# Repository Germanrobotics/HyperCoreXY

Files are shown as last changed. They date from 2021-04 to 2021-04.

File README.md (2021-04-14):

# HyperCoreXY

The HyperCoreXY is a DIY CoreXY Printer which aims for a large workspace while maintaining high printing speeds.

## Specification

- Stable aluminum extrusion frame
- Controlled via a Duet 2 Board
- Powerful 230V heated bed
- Print volume of 390x340x230mm
- Print speeds up to 80-100mm/s

## Todo

- [ ] BOM of all components used
- [ ] Complete assembly instructions
- [ ] A Housing for all electronics to clean things up
- [ ] Reduction of the weight of the Y-axis + Extruder to allow higher printing speeds

## Build Guide

Until I created assembly instructions, you will need to assemble the printer using these videos

**Part 1 Main Mechnical Assembly**
https://www.youtube.com/watch?v=HaM37b0eBO4

**Part 2 Electrical Assembly and first test**
https://www.youtube.com/watch?v=nZ0KHetVHEs

**Part 3 First Prints**
https://www.youtube.com/watch?v=0dgUXOkC-as

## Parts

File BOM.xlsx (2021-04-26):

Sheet: Printed Parts
Name | Description | Qty | Material
Printbed
Connectors print bed |  | 2 | PLA
Connectors print bed mirrored |  | 2 | PLA
Frame
Connector profile |  | 2 | PLA
Housing electronics |  | 1 | PLA
Extruder
Belt Tensioner |  | 2 | PLA
Cable holder |  | 1 | PLA
Cover holder extruder |  | 1 | PLA
Fan duct mirrored |  | 1 | PLA
Fan duct |  | 1 | PLA
Fan holder mirrored |  | 1 | PLA
Fan holder |  | 1 | PLA
Holder belt |  | 4 | PLA
Holder extruder |  | 1 | PLA
Holder hotend |  | 1 | PLA
Spacer 10mm |  | 2 | PLA
X-Axis
End stop X-axis |  | 1 | PLA
Y-Axis
Belt guide left |  | 1 | PLA
Belt guide right |  | 1 | PLA
Holder limit switch Y-axis |  | 2 | PLA
Holder X-axis |  | 2 | PLA
Motor holder left part 1 |  | 1 | PLA
Motor holder left part 2 |  | 1 | PLA
Motor holder right part 1 |  | 1 | PLA
Motor holder right part 2 |  | 1 | PLA
Spacer 6mm |  | 2 | PLA
Z-Axis
Holder bearing spindle |  | 2 | PLA
Holder limit switch Z-axis |  | 1 | PLA
Holder linear rails long |  | 1 | PLA
Holder linear rails |  | 2 | PLA
Motor holder Z-axis |  | 1 | PLA
Other Parts
Adapter 3mm to 5mm |  | 5 | PLA
Adapter 6 to 8mm | If you use the same motors as I do, you will need these | 3 | PLA

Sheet: Hardware
Name | Description | Qty
Angle 20x20 | For the aluminum extrusion | 32
Slot nuts M3 | More then needed | 100
Slot nuts M5 | More then needed | 150
Aluminum plate 430x430mm | 3 or 4mm thick, used as printbed | 1
Spring 20x7.5mm | Needed for the bed | 4
Nanotec 4T5618S2404-A | Stepper motor, but you can also use a Nema 17 or 23, but then you have to change the motor mounts | 4
Micro switches PANASONIC AV3724613-A | or similar, but you may need to adjust the mounts | 3
Belt pulley GT2 20T 8mm | used on motors and spindles, needs the 6mm to 8mm adapter, if you use nema 17 or 23 stepper, you need a different adapter | 5
Belt Idler GT2 20T 3mm | Idler with tooths | 6
Idler GT2 5mm | Idler without tooths, needs the 5mm to 3mm adapter | 5
Lead screw 350mm | 8mm diameter, I got a set with two horizontal bearings, you may need to buy them separately | 2
Linear bearing 350mm | MGN12H Linear bearings with one wagon | 3
Linear bearing 450mm | MGN12H Linear bearings with one wagon | 3
GT2 Belt 1000mm 500T | Closed GT2 Belt with 500Tooths, 1000mm long | 1
Bondtech BMG Extruder right | or a clone | 1
E3D Volcano Hotend Direct Drive | 12V Kit or a clone | 1
Nema 17 Pancake Stepper | used for the BMG Extruder | 1
PTFE Tubing | PTFE Tubing 1.75mm, you need around 80cm | 1
BL Touch | not necessary, but simplifies bedleveling | 1
GT2 Belt open | measured in meters | 6
Radial Fans | 5015 12V Radial Fans, used for part cooling | 2
Cylinder head screw M3x35 | More then needed | 50
Cylinder head screw M3x8 | More then needed | 100
Cylinder head screw M3x20 | More then needed | 50
Cylinder head screw M4x45 | More then needed | 50
Cylinder head screw M5x10 | More then needed | 150
Duet 2 Ethernet Board |  | 1
Power supply 12V 20A 240W | probably way too big, but it was the smallest I found | 1
Heated bed 220V 650W 408x408mm | i bought a yourDroid silicone heat bed | 1
Solid State Relay 220V 40A |  | 1

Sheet: Aluminum extrusion
Name | Length | Qty | I bought 11 1 meter long 20x20 Alumimun profiles and then cut them to length
Profil Print bed 1 | 420 | 2
Profil Print bed 2 | 350 | 2
Profil Frame 1 | 550 | 4
Profil Frame 2 | 370 | 3
Profil Frame 3 | 440 | 4
Profil Frame 4 | 520 | 5
Profil X-Axis | 510 | 1

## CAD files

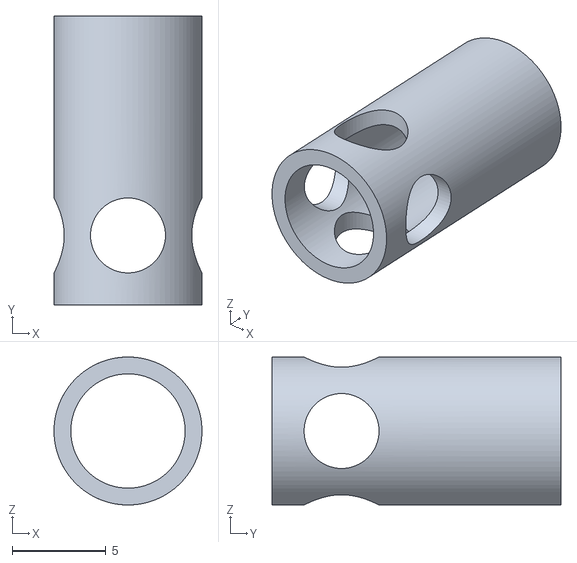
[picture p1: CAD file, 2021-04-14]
files/Adapter/Adapter 6 to 8mm.stl
7.90 x 15.4 x 7.90

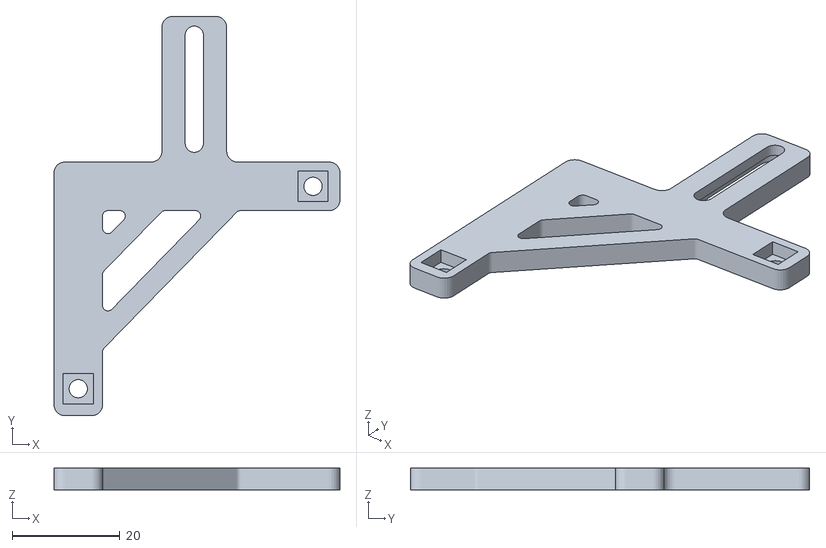
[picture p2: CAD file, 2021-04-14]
files/Extruder/Fan holder mirrored.stl
53.0 x 74.0 x 4.00

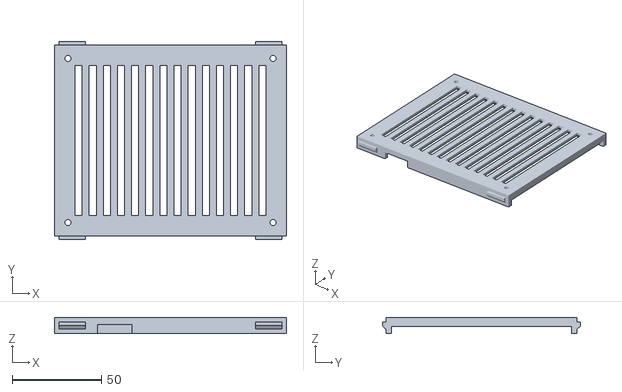
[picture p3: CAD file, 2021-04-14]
files/Frame/Housing electronics.stl
130.0 x 111.0 x 9.00

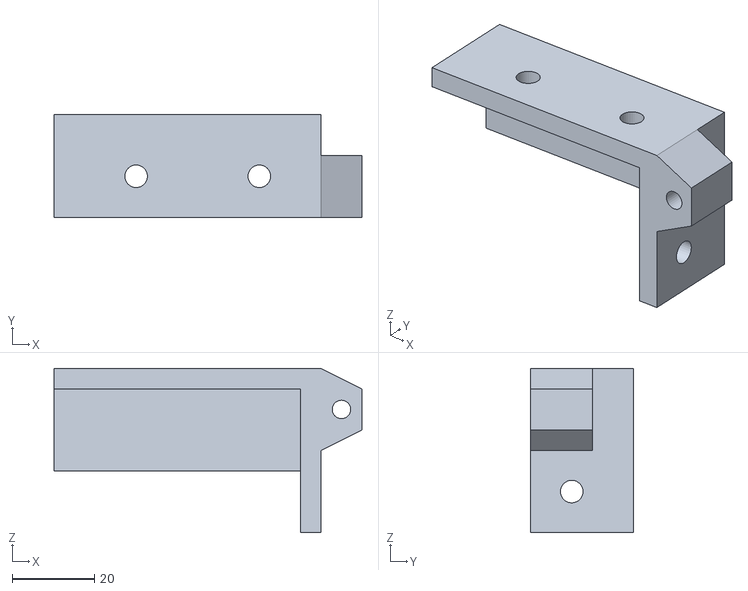
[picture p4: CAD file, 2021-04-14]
files/Print bed/Connectors print bed.stl
75.0 x 25.0 x 40.0

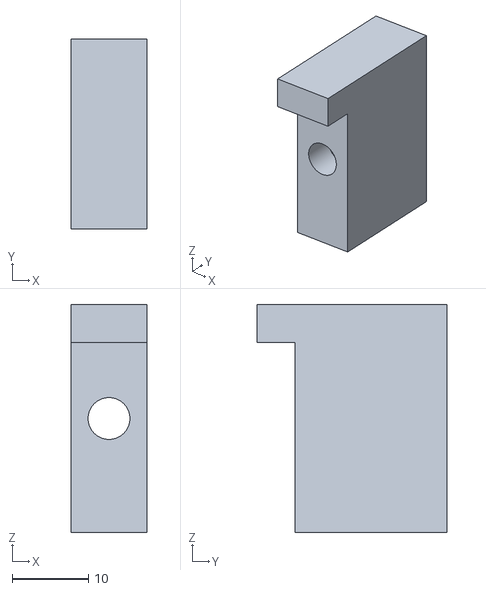
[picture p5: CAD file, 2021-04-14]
files/X-Axis/End stop X-axis.stl
10.0 x 25.0 x 30.0

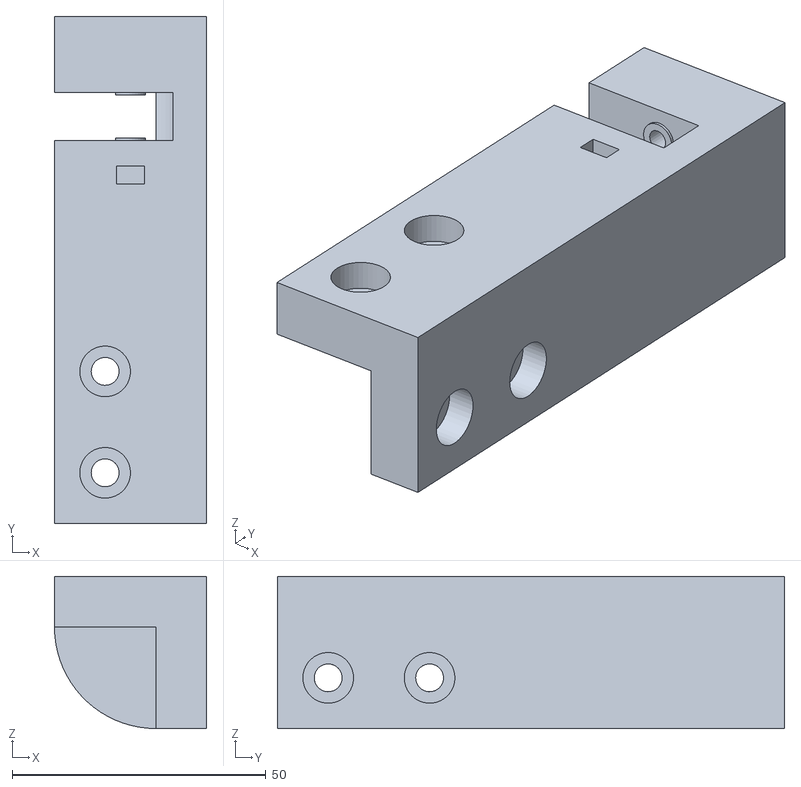
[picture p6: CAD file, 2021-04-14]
files/Y-Axis/Belt guide right.stl
30.0 x 100.0 x 30.0

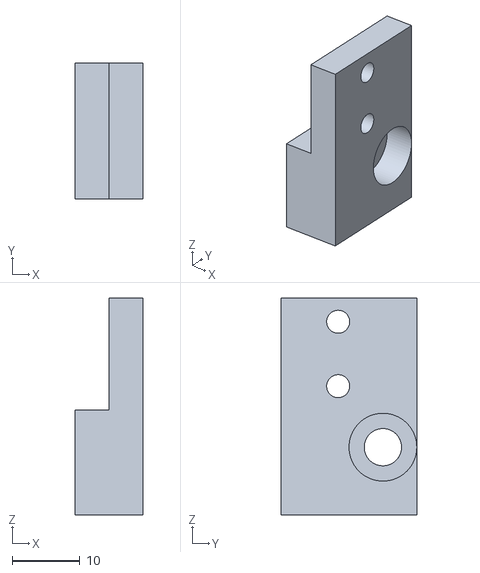
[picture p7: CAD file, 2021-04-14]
files/Z-Axis/Holder limit switch Z-axis.stl
10.0 x 20.0 x 32.0

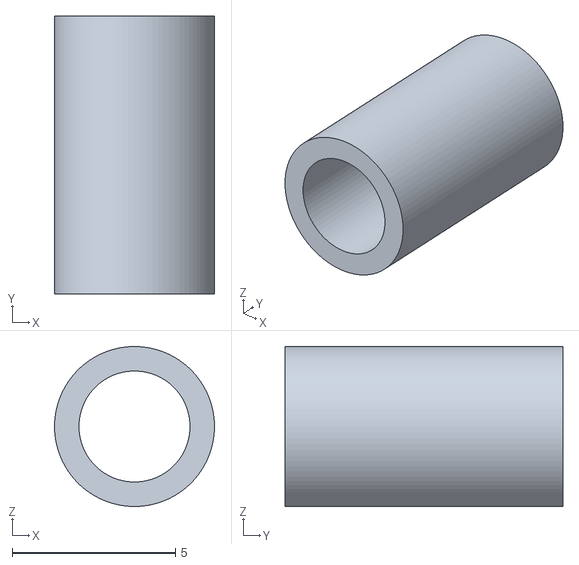
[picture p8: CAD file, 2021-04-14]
files/Adapter/Adapter 3mm to 5mm.stl
4.90 x 8.50 x 4.90

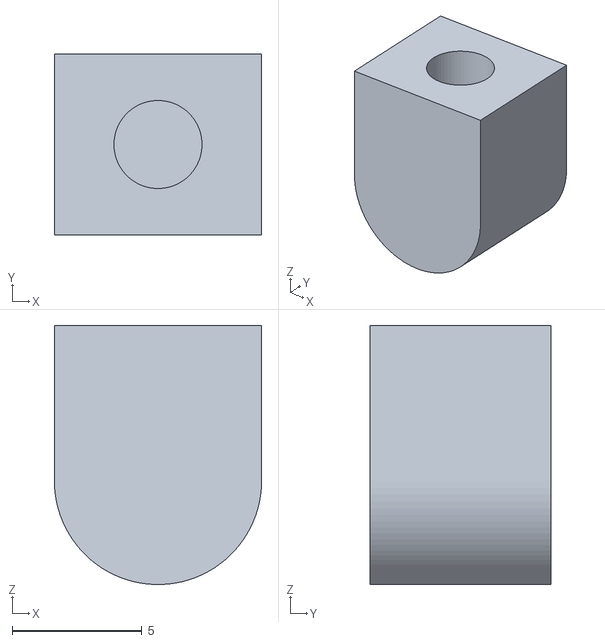
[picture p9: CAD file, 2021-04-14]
files/Extruder/Belt Tensioner .stl
8.00 x 7.00 x 10.00

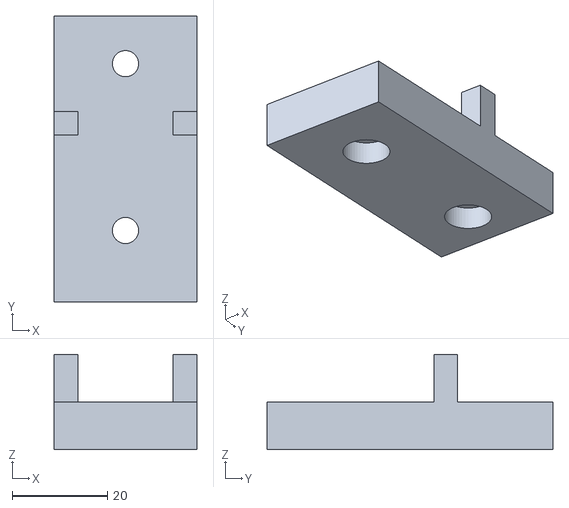
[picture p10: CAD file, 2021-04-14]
files/Frame/Connector profile.stl
30.0 x 60.0 x 20.0

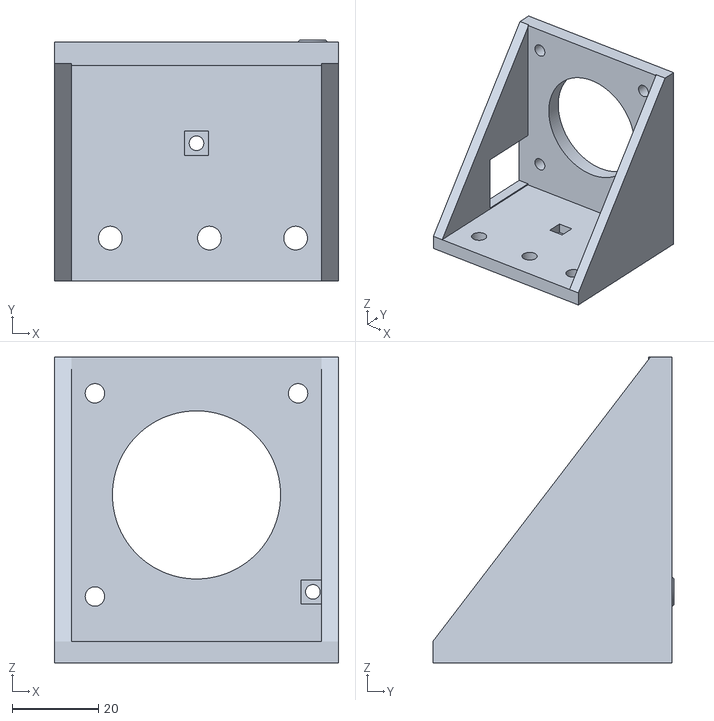
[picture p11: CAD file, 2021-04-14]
files/Y-Axis/Motor holder left part 1.stl
66.0 x 56.0 x 71.0

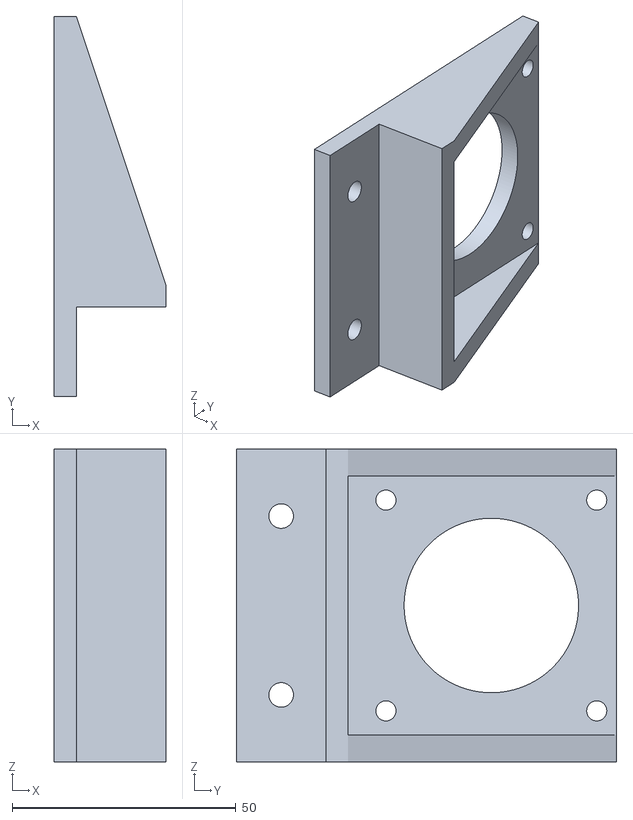
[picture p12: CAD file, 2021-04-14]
files/Z-Axis/Motor holder Z-axis.stl
25.0 x 85.0 x 70.0

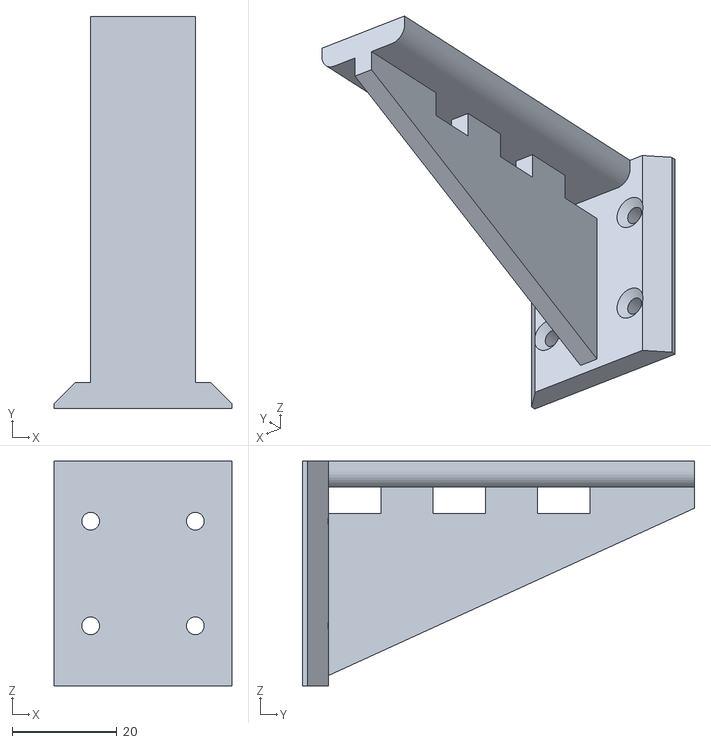
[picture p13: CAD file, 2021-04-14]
files/Extruder/Cable holder.stl
34.0 x 75.0 x 43.0

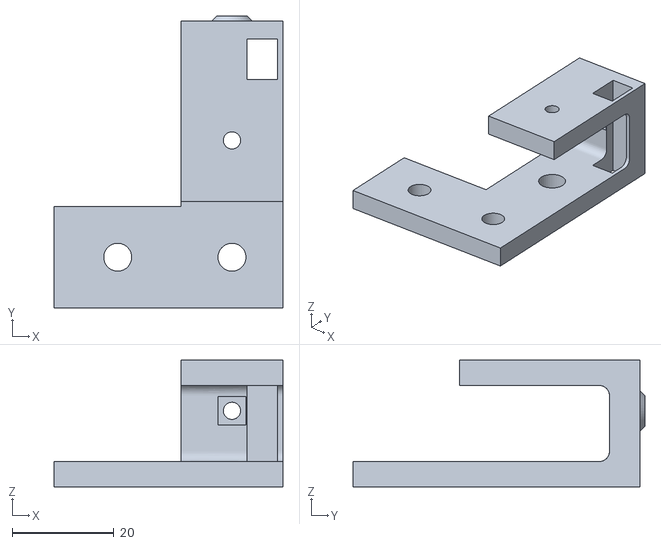
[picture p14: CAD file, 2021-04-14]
files/Y-Axis/Motor holder right part 2.stl
45.0 x 57.5 x 25.0

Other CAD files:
files/Print bed/Connectors print bed mirrored.stl
files/Z-Axis/Holder linear rails long.stl
files/Extruder/Holder belt.stl
files/Y-Axis/Holder X-axis.stl
files/Extruder/Cover holder extruder.stl
files/Extruder/Fan duct mirrored.stl
files/Extruder/Fan duct.stl
files/Extruder/Fan holder.stl
files/Extruder/Holder extruder.stl
files/Extruder/Holder hotend.stl
files/Extruder/Spacer 10mm.stl
files/Y-Axis/Belt guide left.stl
files/Y-Axis/Holder limit switch Y-axis.stl
files/Y-Axis/Motor holder left part 2.stl
files/Y-Axis/Motor holder right part 1.stl
files/Y-Axis/Spacer 6mm.stl
files/Z-Axis/Holder bearing spindle.stl
files/Z-Axis/Holder linear rails.stl

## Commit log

2021-04-14 Uploade files
    [Adapter 3mm to 5mm.stl, Adapter 6 to 8mm.stl, Belt Tensioner .stl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]
2021-04-26 Added BOM
    [BOM.xlsx]
